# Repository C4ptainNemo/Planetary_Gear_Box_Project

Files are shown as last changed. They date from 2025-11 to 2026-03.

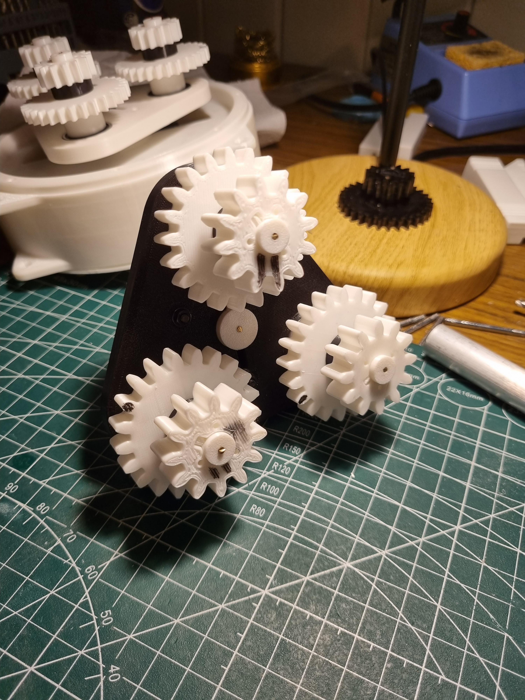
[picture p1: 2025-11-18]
PICTURES_&_DIAGRAMS/20250924_110358.jpg

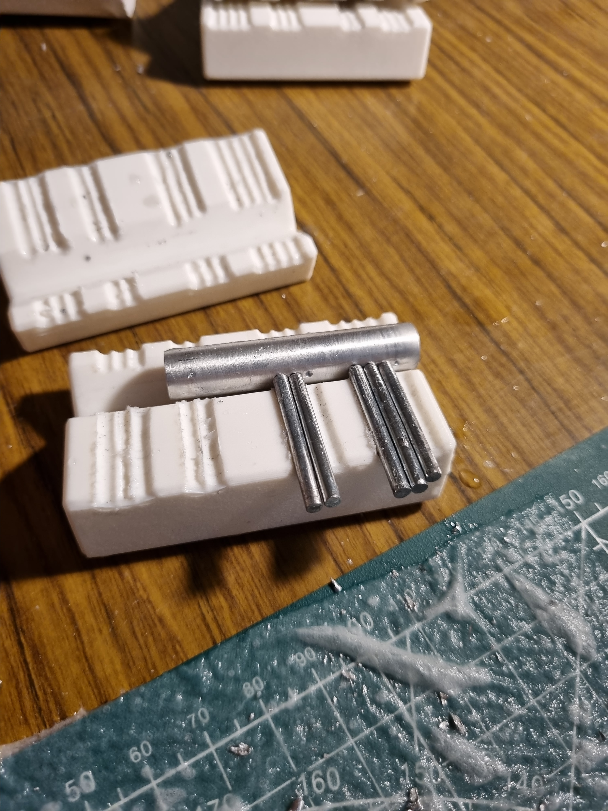
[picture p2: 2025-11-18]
PICTURES_&_DIAGRAMS/20250923_115708.jpg

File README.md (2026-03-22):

# Planetary Gear Box Project
gearbox
A Two Stage Compound Planetary Gearbox designed and built for a university design project. All content contained here was done by myself unless otherwise stated.  

The project required a gearbox that would output 20 Nm of torque and have a 65x speed reduction. This was a group project done with three others, however I did all of the CAD except for some of the technical drawings (though I have included here my own versions).

I wrote a MATLAB script to help find a solution that optimised the design to have the minimum sized gearbox. The limiting factor in the size was the minimum advised gear module (1.5) using laminated lasercut acrylic to form the gears. I will note that the code isn't very good and required some adjustment of the solution that the main script output, but it gave a decent solution that was mostly the smallest it could possibly be. The search isn't very exhaustive either, and the checks for the validity of a solution are not very compregensive nor easy to update.

My individual design is similar to the final group version that was built, with the second stage of the individual design being the same as both stages on the group design. Referencing the appendix in the individual report shows the calculations used for the individual and group gearbox.

The process of designing and building the gearbox involved:  
  1. Calculations to solve for the sun gear module of a stage (which dictated the other gear modules), given various parameters such as output torque, input speed, teeth count of all gears, factor of safety, etc.  
  2. Writing the MATLAB scripts to find a solution that minimised the size of the gearbox.  
  3. 3D printing all the parts of the gearbox, including shafts and gears to validate assembly and function, and to inform any changes that were needed.  
  4. Manufacturing the non-3D printed parts and 1-for-1 swapping them for their 3D printed counterparts.

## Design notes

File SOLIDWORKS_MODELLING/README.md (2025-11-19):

# SolidWorks Model
This is the SolidWorks directory for the gearbox assembly, subassembly and parts.  
You should just be able to download the whole directory and the relative filepaths should work fine.

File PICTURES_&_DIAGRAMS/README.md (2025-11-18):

# Pictures and Diagrams
The pictures are of the fully 3D printed prototype, as I neglected to take any of the completed gearbox (this was a lesson learned).  
The videos are of the completed gearbox with aluminium shafts and acrylic gears.

Diagrams.pptx was used to create various diagrams for the group report.
I built a basic model of the gearbox in Fusion360 (I'm more familar, and it is easier to build a simple assembly), and exported the drawings to crop and paste into Powerpoint. 
The SFD, BMD and TD plots were made with MATLAB since I'm more familiar with creating complicated plots using it.

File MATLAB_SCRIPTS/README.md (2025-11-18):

# MATLAB SCRIPTS
**1. gear_calculations.m** - The main script that takes input parameters and outputs an optimal solution.  
**2. calculate_gears.m** - Function script that does all the calculations.  
**3. individual_calculation.m** - Script that allows for inputting any number of gear teeth. This was to allow modifying a solution given by the main script.  
**4. Shaft_Force_Diagram_Plots.m** - Script for generating shaft shear force, bending moment and torque diagrams.  
**5. 251004-Planet_Gear_Table.pdf** - Gear table, showing the details about each stage.

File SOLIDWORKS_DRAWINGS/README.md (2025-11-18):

# SOLIDWORKS DRAWINGS
These are the technical drawings from SolidWorks for the gearbox. I did all of the modelling, and some of the drawings that were submitted in the report (I included my own versions here for the sake of completion).

The drawings were broken down into letter coded sections. This made it easier to delegate subassembelies and combine the individual drawings into one for the group report.

* **[A: Top Level Assembly](Top_Level_Assembly_Drawings.pdf)**
* **[B: Front Housing](Housing_Front_Assembly.pdf)**
* **[C: Middle Housing & Housing Alignment Rod](Housing_Centre_Assembly.pdf)**
* **[D: Rear Housing](Housing_Back_Assembly.pdf)**
* **[E: Stage 1 Carrier](Carrier_Stage_1.pdf)**
* **[F: Stage 2 Carrier](Carrier_Stage_2.pdf)**
* **[G: Stand](Stand_Assembly.pdf)**
* **[H: Other Parts, used in assembly](Other%20Parts.pdf)**

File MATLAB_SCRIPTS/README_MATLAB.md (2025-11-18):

1. gear_calculations - The main script that takes input parameters and outputs an optimal solution.
2. calculate_gears - Function script that does all the calculations.
3. individual_calculation - Script that allows for inputting any number of gear teeth. This was to allow modifying a solution given by the main script.
4. 251004-Planet_Gear_Table - Gear table, showing the details about each stage.

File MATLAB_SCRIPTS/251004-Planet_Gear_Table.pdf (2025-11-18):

Overall Details
Gear_ratio_total | Eff._total
________________ | __________
65.143 | 0.47292

Stage 1
Gear | | Teeth | Module_mm | Diameter_mm | Face_Width_mm | Lewis_Form_Factor | Stress_MPa | Factor_Safety | Tan._Force_N | Rad._Force_N | Torque_Nm | RPM | Power_W | V_rel_m_s
____________ | _____ | _________ | ___________ | _____________ | _________________ | __________ | _____________ | ____________ | ____________ | _________ | _______ | _______ | _________
{'Sun' | } | 15 | 1.6722 | 25.083 | 6 | 0.289 | 5.9505 | 10.083 | 17.254 | 6.2801 | 0.6492 | 1500 | 101.98 | 1.97
{'Planet 1'} | 30 | 1.6722 | 50.167 | 6 | 0.358 | 3.2661 | 18.37 | 11.732 | 4.27 | 0.29427 | -503.91 | 15.528 | 1.3236
{'Ring' | } | 57 | 1.75 | 99.75 | 6 | 0.4174 | 3.7268 | 16.1 | 16.333 | 5.9449 | 2.4439 | 0 | 0 | 0
{'Planet 2'} | 14 | 1.75 | 24.5 | 6 | 0.276 | 8.2892 | 7.2383 | 24.022 | 8.7434 | 0.29427 | -503.91 | 15.528 | 0.64642
{'Carrier' } | NaN | NaN | 75.25 | NaN | NaN | NaN | NaN | 35.754 | NaN | 4.0357 | 164.06 | 69.336 | 0.64642
Gear_Ratio | Planet_Diamater_mm | Overall_Diameter_mm | Eff._Mesh | Eff._Ack | Num_Planets | Safety_Factor | S_y_MPa | Pressure_Angle_deg
__________ | __________________ | ___________________ | _________ | ________ | ___________ | _____________ | _______ | __________________
9.1429 | 125.42 | 125.42 | 0.75 | 0.67993 | 3 | 3 | 60 | 20

Stage 2
Gear | | Teeth | Module_mm | Diameter_mm | Face_Width_mm | Lewis_Form_Factor | Stress_MPa | Factor_Safety | Tan._Force_N | Rad._Force_N | Torque_Nm | RPM | Power_W | V_rel_m_s
____________ | _____ | _________ | ___________ | _____________ | _________________ | __________ | _____________ | ____________ | ____________ | _________ | _______ | _______ | _________
{'Sun' | } | 12 | 2.2727 | 27.273 | 9 | 0.245 | 19.686 | 3.0479 | 98.651 | 35.906 | 4.0357 | 164.06 | 69.336 | 0.23428
{'Planet 1'} | 21 | 2.2727 | 47.727 | 9 | 0.325 | 10.322 | 5.813 | 68.616 | 24.974 | 1.6374 | -57.566 | 9.8709 | 0.14386
{'Ring' | } | 42 | 2.5 | 105 | 9 | 0.393 | 8.5865 | 6.9877 | 75.926 | 27.635 | 11.958 | 0 | 0 | 0
{'Planet 2'} | 12 | 2.5 | 30 | 9 | 0.245 | 19.803 | 3.0299 | 109.16 | 39.732 | 1.6374 | -57.566 | 9.8709 | 0.090424
{'Carrier' } | NaN | NaN | 75 | NaN | NaN | NaN | NaN | 177.78 | NaN | 20 | 23.026 | 48.226 | 0.090424
Gear_Ratio | Planet_Diamater_mm | Overall_Diameter_mm | Eff._Mesh | Eff._Ack | Num_Planets | Safety_Factor | S_y_MPa | Pressure_Angle_deg
__________ | __________________ | ___________________ | _________ | ________ | ___________ | _____________ | _______ | __________________
7.125 | 122.73 | 122.73 | 0.75 | 0.69554 | 3 | 3 | 60 | 20

>>

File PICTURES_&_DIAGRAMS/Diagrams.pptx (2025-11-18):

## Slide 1

y

x

F_(R,s)

F_(t,s)

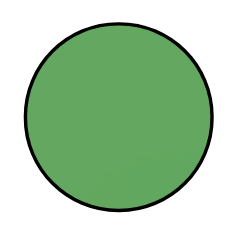
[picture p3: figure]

ω_s , T_s

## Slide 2

y

x

F_(t,c)

F_(t,c)

ω_s , T_s

r_c

F_(t,c)

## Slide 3

y

x

F_(R,p_2)

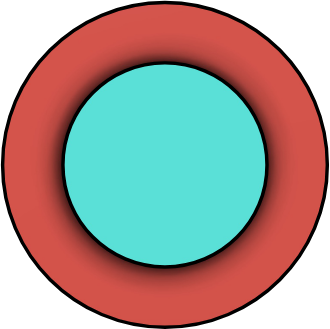
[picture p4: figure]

F_(t,p_2)

F_(t,c)

F_(t,p_1)

ω_s

ω_p

F_(R,p_1)

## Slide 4

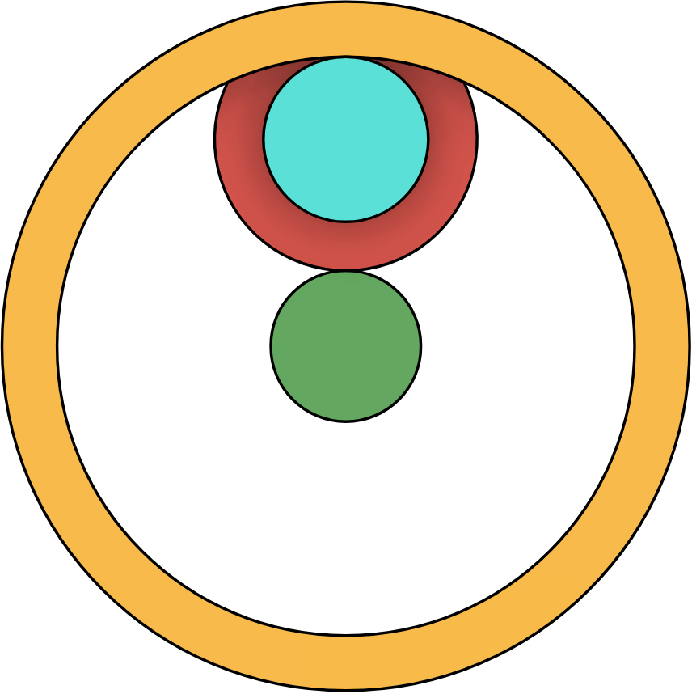
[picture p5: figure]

r_(p_2)

r_(p_1)

r_r

r_s

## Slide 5

F_(R,p_2)

F_(t,p_2)

y

x

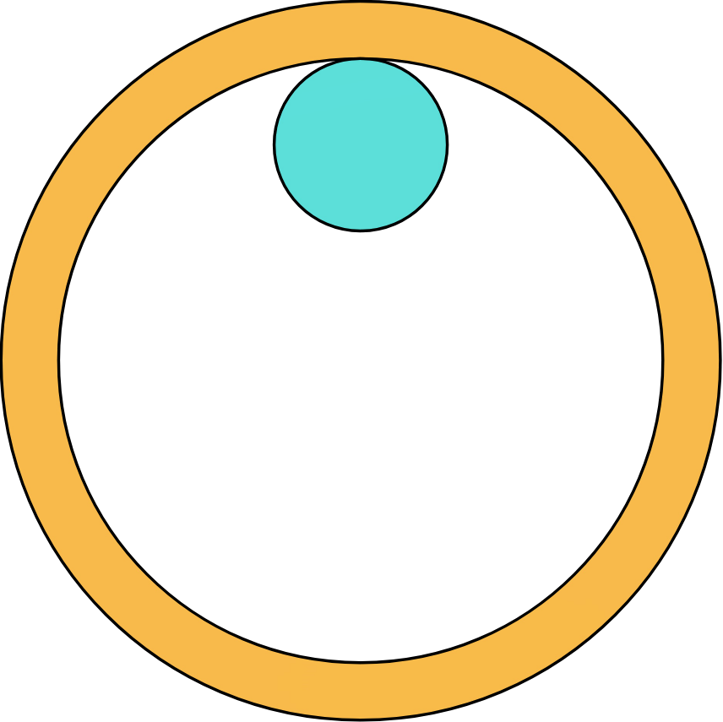
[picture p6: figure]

F_(t,r)

F_(R,r)

ω_p

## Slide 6

y

x

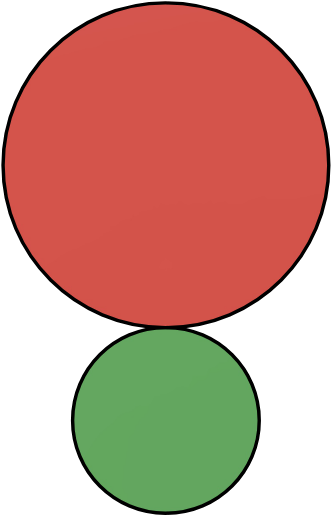
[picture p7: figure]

v_c

ω_c

v_p^(′)

ω_s

ω_p

v_s

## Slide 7

y

x

v_p^(′)

ω_c

v_c

ω_p

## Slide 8

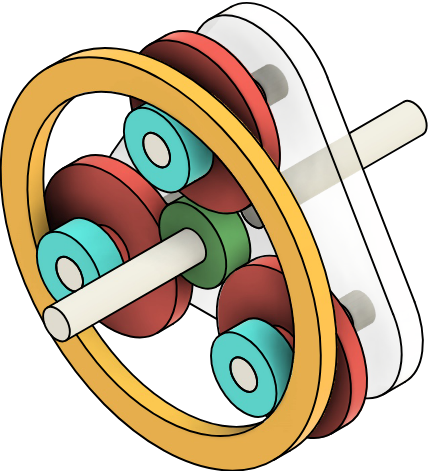
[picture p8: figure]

y

x

z

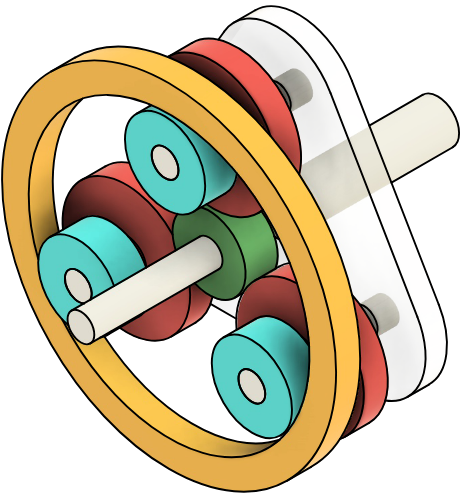
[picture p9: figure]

y

x

z

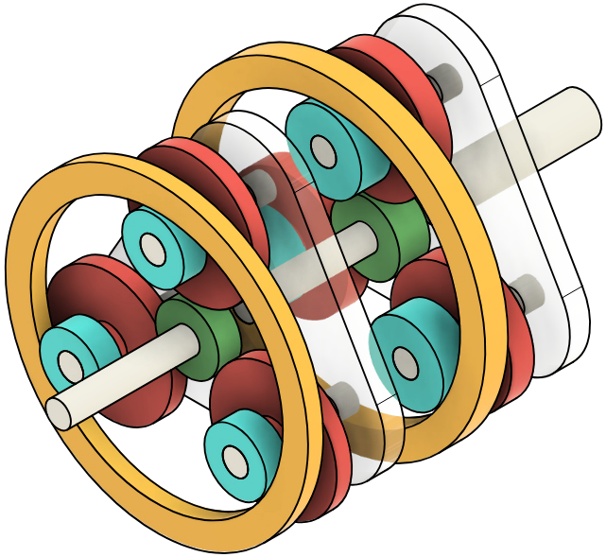
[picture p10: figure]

y

x

z

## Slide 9

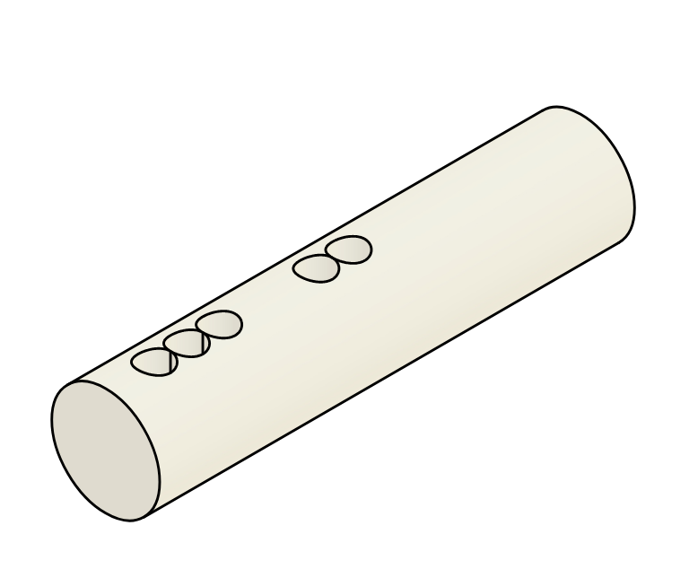
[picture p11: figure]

y

x

z

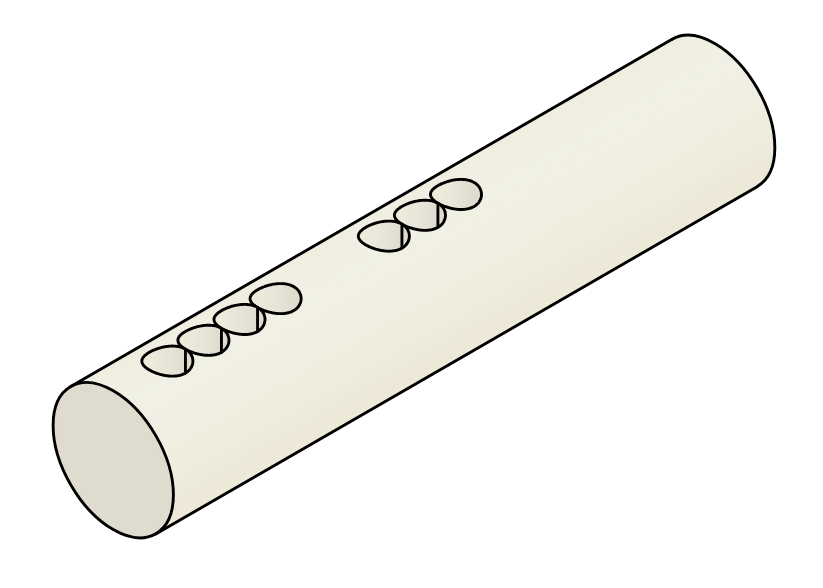
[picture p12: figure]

y

x

z

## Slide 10

y

y

z

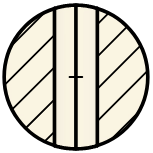
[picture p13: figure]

z

y

z

x

z

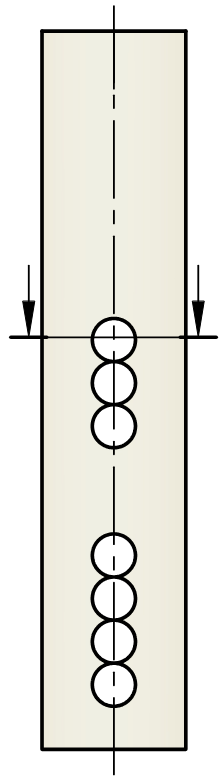
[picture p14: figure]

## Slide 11

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
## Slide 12

y

x

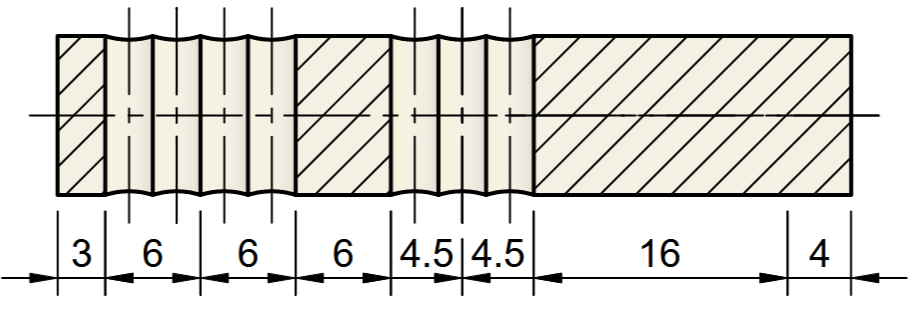
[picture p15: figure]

y

x

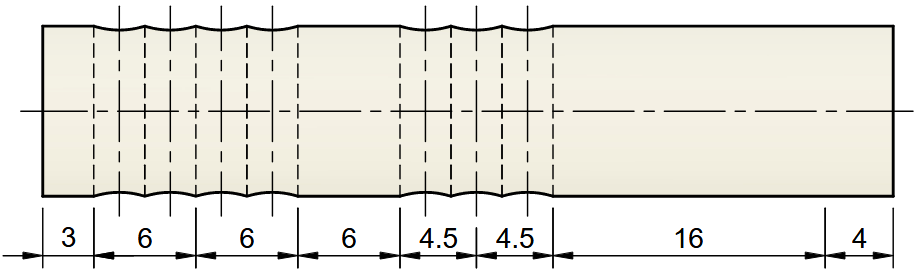
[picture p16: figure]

x

z

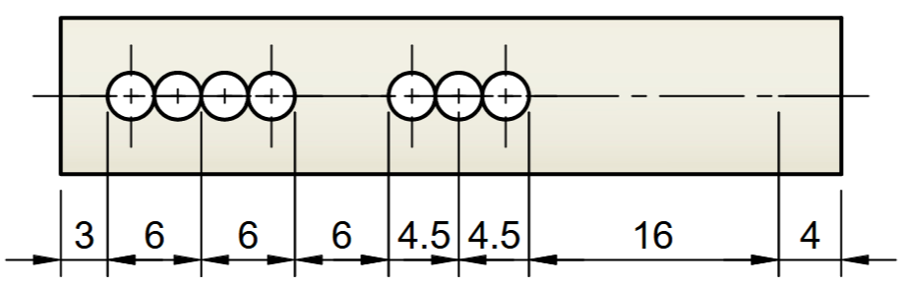
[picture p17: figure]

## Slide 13

y

x

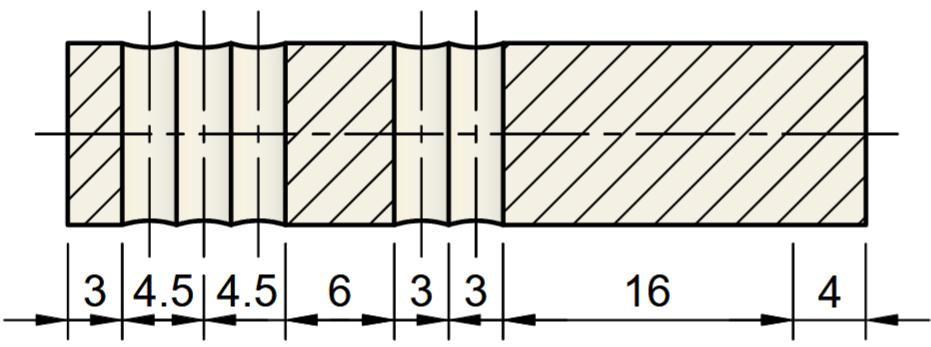
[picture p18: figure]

y

x

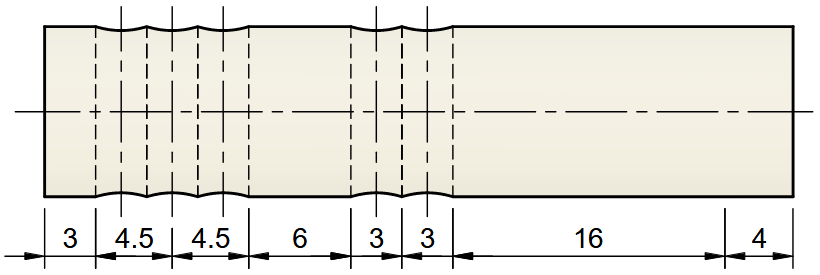
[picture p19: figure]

x

z

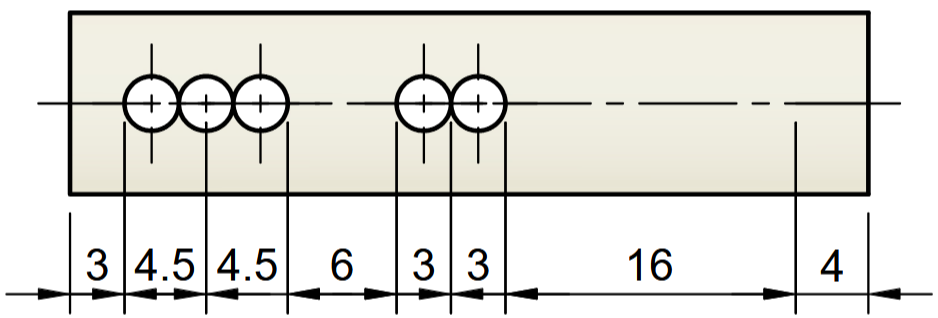
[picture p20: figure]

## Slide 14

y

x

y

x

y

x

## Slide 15

y

x

F_(R,p_2)

F_(R,p_1)

R_y

M_(D,z)

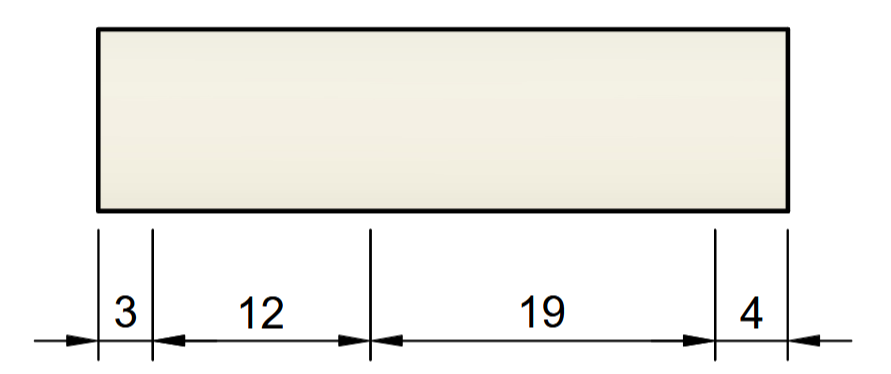
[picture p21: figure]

A

B

C

D

R_x

T_(p_2)

T_(p_1)

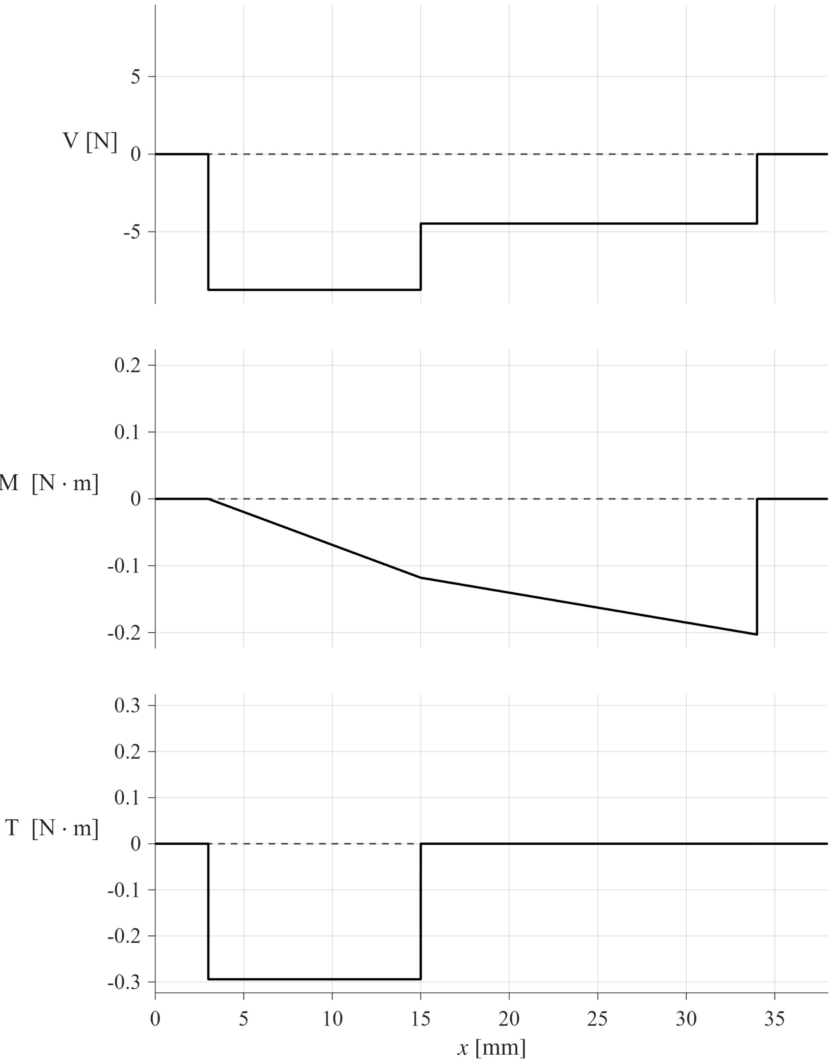
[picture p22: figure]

7.5

13.5

19

4

x

z

F_(t,p_2)

F_(t,p_1)

R_z

M_(D,y)

R_x

A

B

C

D

T_(p_2)

T_(p_1)

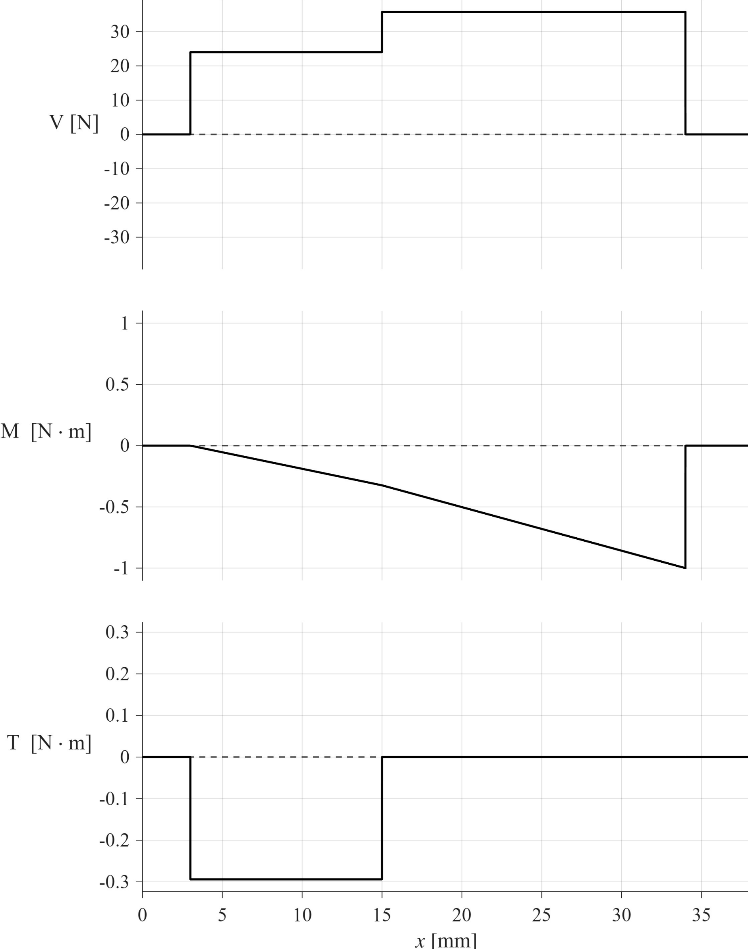
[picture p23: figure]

7.5

13.5

19

4

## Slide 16

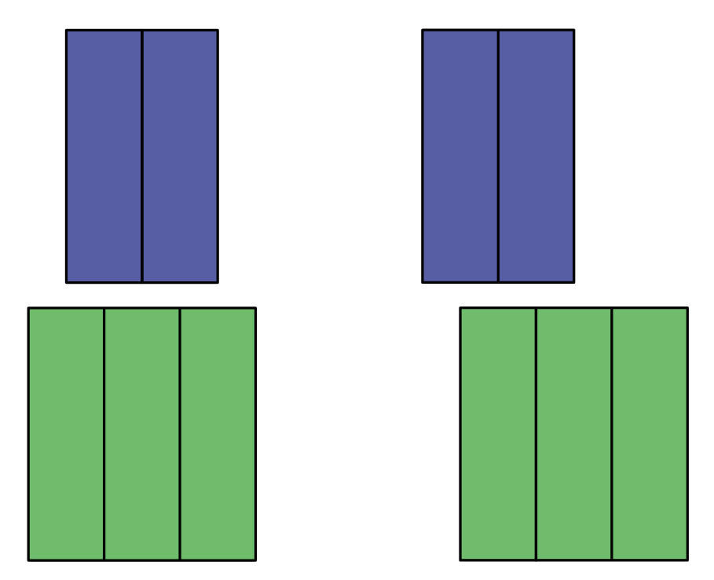
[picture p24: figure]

Aligned

Misaligned

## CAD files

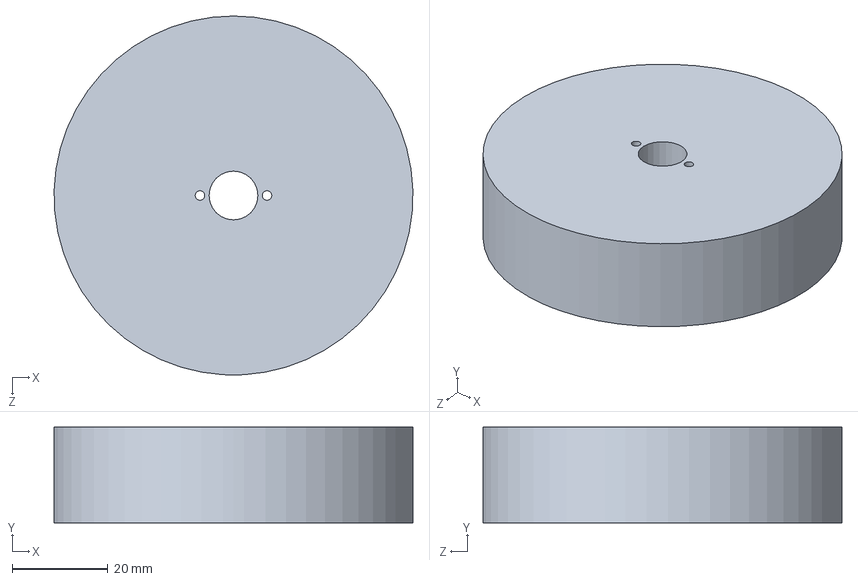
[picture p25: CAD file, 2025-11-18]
SOLIDWORKS_MODELLING/Assembly Parts/Gear Assembly Stand.SLDPRT
75.0 x 20.0 x 75.0 mm

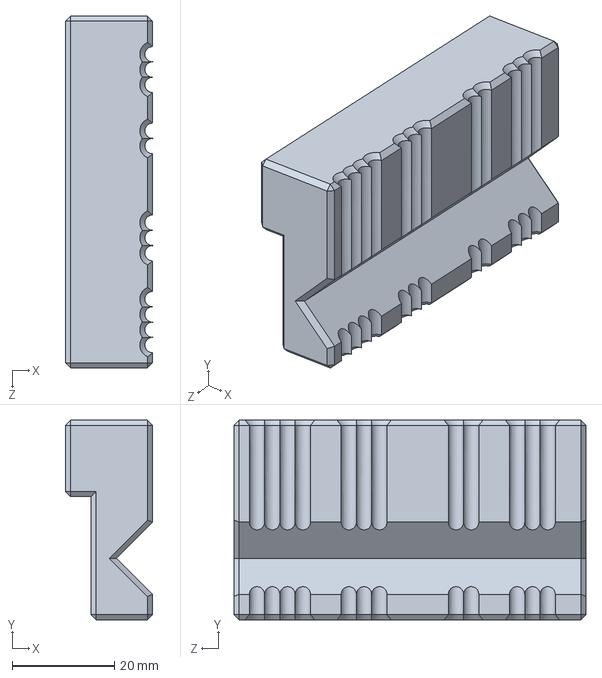
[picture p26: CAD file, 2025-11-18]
SOLIDWORKS_MODELLING/Assembly Parts/Drill Hole Guide.SLDPRT
17.1 x 39.1 x 69.0 mm

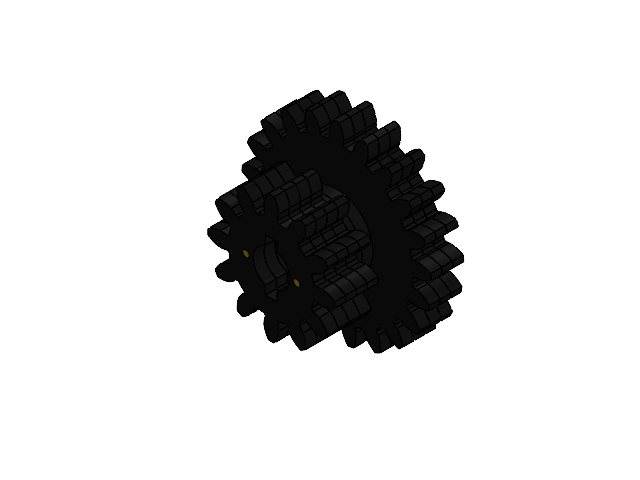
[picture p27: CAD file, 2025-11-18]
SOLIDWORKS_MODELLING/Assemblies/Gears/Planet_Gear_Stage_2.SLDASM
External_Spur_Gear x 7
Spacer x 2
Alignment_Pin x 2

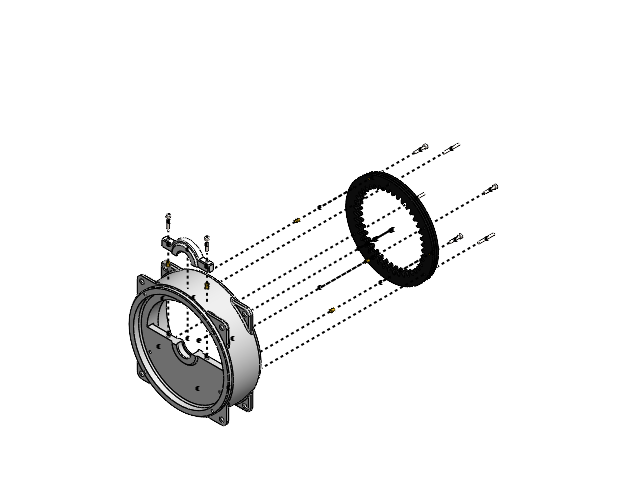
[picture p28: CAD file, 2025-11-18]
SOLIDWORKS_MODELLING/Assemblies/Housing_Centre_Assembly.SLDASM
Housing_Centre
Housing_Bearing_Cover
Threaded_Heat_Insert_M3x5.7x4.6 x 5
Internal_Spur_Gear_Stage_2 x 3
Alignment_Pin x 3
socket head cap screw_iso x 5
Ring_Gear_Alignment_Pin x 3

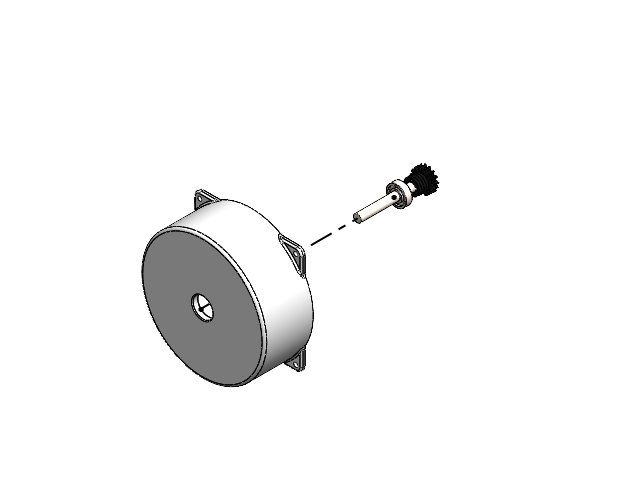
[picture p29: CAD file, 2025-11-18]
SOLIDWORKS_MODELLING/Gearbox-2_Stage-Planetary_Compound-65_Reduction.SLDASM
Housing_Front
Threaded_Heat_Insert_M3x5.7x4.6 x 3
Internal_Spur_Gear_Stage_1 x 2
Alignment_Pin x 5
socket head cap screw_iso x 3
Ring_Gear_Alignment_Pin x 3
Shaft_KeyPins_SingleEnded
Key_Pin_3mm x 3
External_Spur_Gear x 3
Spacer x 4
radial ball bearing_68_skf

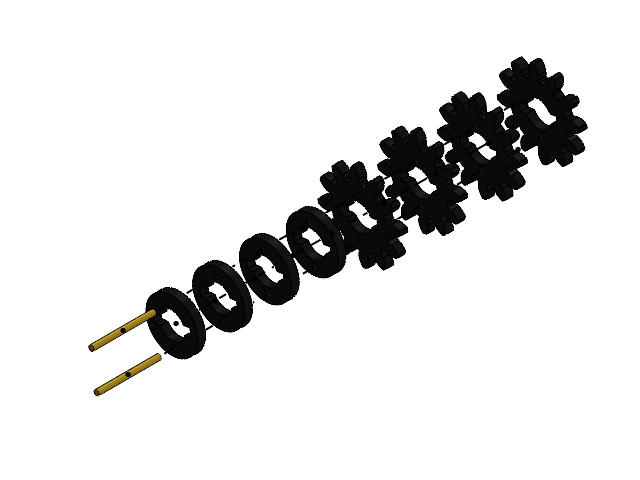
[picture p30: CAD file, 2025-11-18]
SOLIDWORKS_MODELLING/Assemblies/Gears/Sun_Gear_2.SLDASM
External_Spur_Gear x 4
Alignment_Pin x 2
Spacer x 4

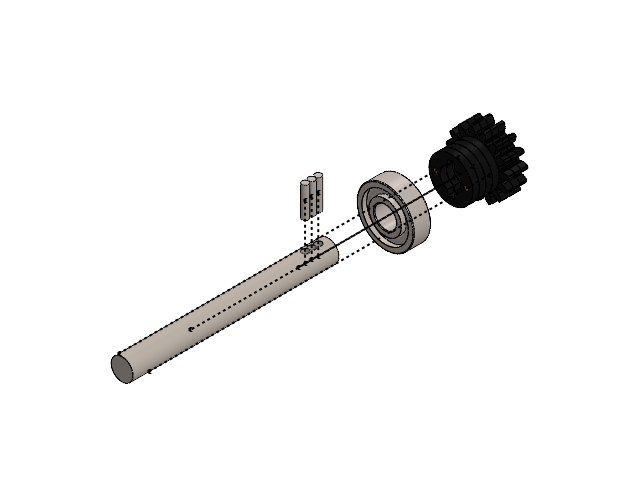
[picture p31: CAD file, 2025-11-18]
SOLIDWORKS_MODELLING/Assemblies/Sun_Gear_Stage_1_Subassembly.SLDASM
Shaft_KeyPins_SingleEnded
Key_Pin_3mm x 3
External_Spur_Gear x 3
Alignment_Pin x 2
Spacer x 4
radial ball bearing_68_skf

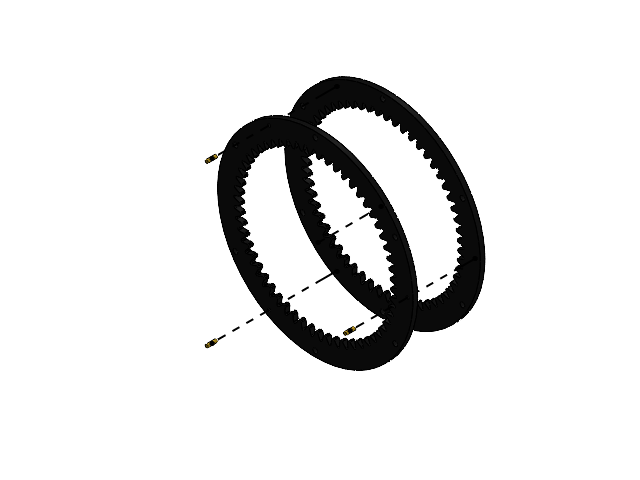
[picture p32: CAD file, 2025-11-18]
SOLIDWORKS_MODELLING/Assemblies/Gears/Ring_Gear_Stage_1.SLDASM
Internal_Spur_Gear_Stage_1 x 2
Alignment_Pin x 3

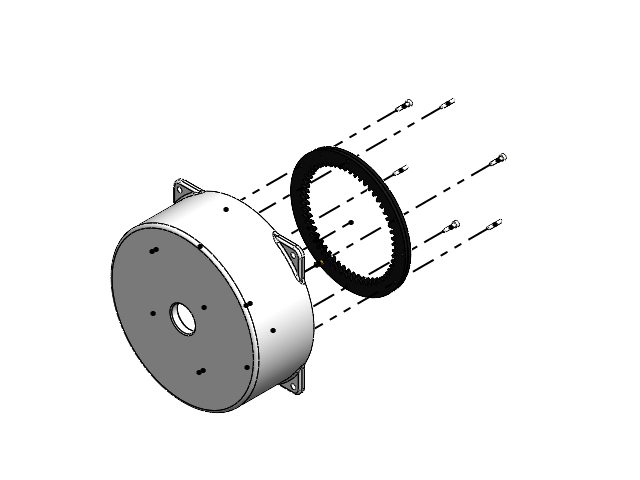
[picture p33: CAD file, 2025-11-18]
SOLIDWORKS_MODELLING/Assemblies/Housing_Front_Assembly.SLDASM
Housing_Front
Threaded_Heat_Insert_M3x5.7x4.6 x 3
Internal_Spur_Gear_Stage_1 x 2
Alignment_Pin x 3
socket head cap screw_iso x 3
Ring_Gear_Alignment_Pin x 3

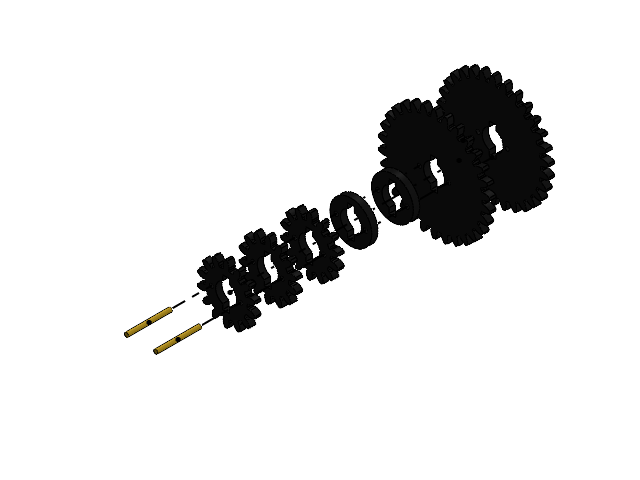
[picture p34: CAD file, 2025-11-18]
SOLIDWORKS_MODELLING/Assemblies/Gears/Planet_Gear_Stage_1.SLDASM
External_Spur_Gear x 5
Spacer x 2
Alignment_Pin x 2

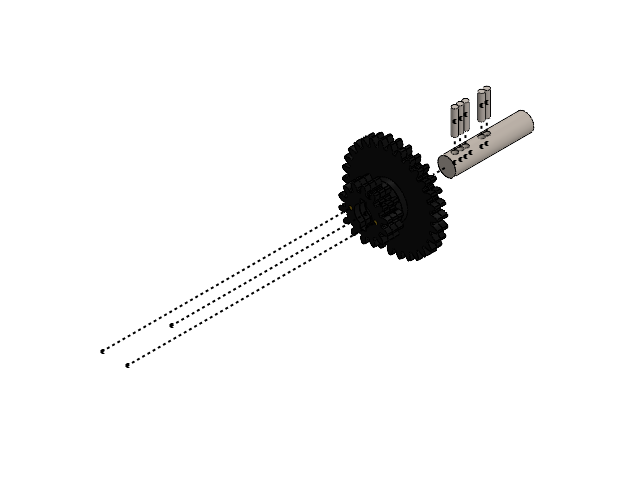
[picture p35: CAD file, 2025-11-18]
SOLIDWORKS_MODELLING/Assemblies/Planet_Gear_Stage_1_Subassembly.SLDASM
Shaft_KeyPins_SingleEnded
Key_Pin_3mm x 5
External_Spur_Gear x 5
Spacer x 2
Alignment_Pin x 2

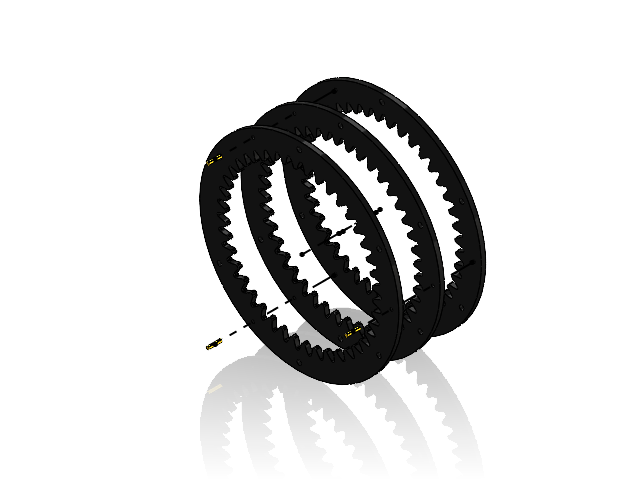
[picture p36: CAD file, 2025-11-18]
SOLIDWORKS_MODELLING/Assemblies/Gears/Ring_Gear_Stage_2.SLDASM
Internal_Spur_Gear_Stage_2 x 3
Alignment_Pin x 3

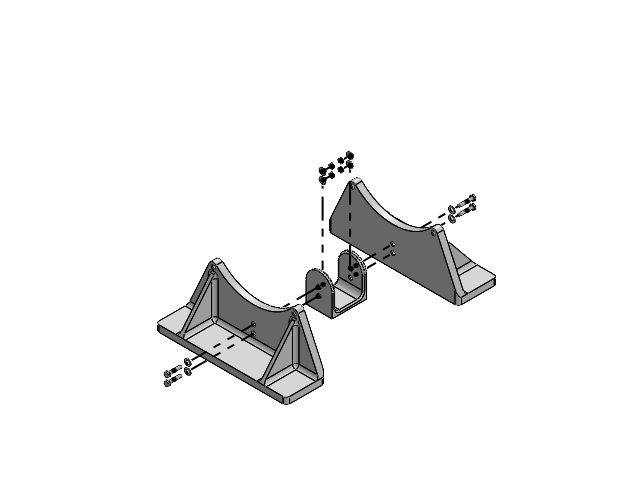
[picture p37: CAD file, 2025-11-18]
SOLIDWORKS_MODELLING/Assemblies/Stand_Assembly.SLDASM
Stand x 2
Stand_Spacer
plain washer 10669 type nl_iso x 8
hex bolt gradeb_iso x 4
hex thin nut chamfered gradeab_iso x 4

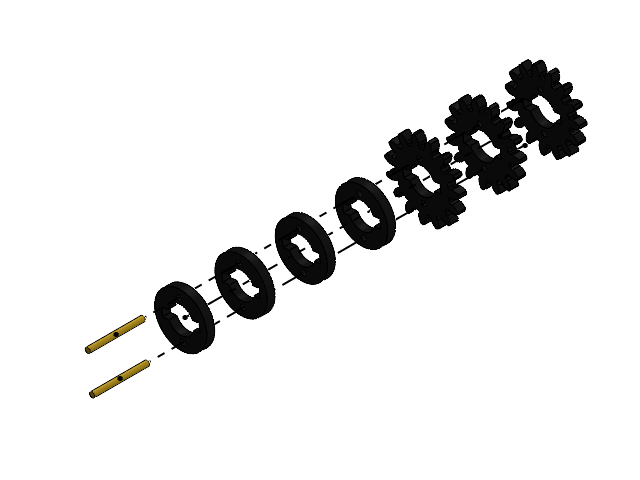
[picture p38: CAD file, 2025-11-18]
SOLIDWORKS_MODELLING/Assemblies/Gears/Sun_Gear_1.SLDASM
External_Spur_Gear x 3
Alignment_Pin x 2
Spacer x 4

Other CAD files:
SOLIDWORKS_MODELLING/Assemblies/Housing_Back_Assembly.SLDASM
SOLIDWORKS_MODELLING/Assemblies/Carrier_Stage_2.SLDASM
SOLIDWORKS_MODELLING/Assemblies/Planet_Gear_Stage_2_Subassembly.SLDASM
SOLIDWORKS_MODELLING/Assemblies/Carrier_Stage_1.SLDASM
SOLIDWORKS_MODELLING/Assembly Parts/12 mm Half Spacer.SLDPRT
SOLIDWORKS_MODELLING/Assembly Parts/Bearing Removal Plate.SLDPRT
SOLIDWORKS_MODELLING/Assembly Parts/Bearing Removal Stand.SLDPRT
SOLIDWORKS_MODELLING/Assembly Parts/Drill Hole Guide Double Ended.SLDPRT
SOLIDWORKS_MODELLING/Assembly Parts/Drill Hole Guide large.SLDPRT
SOLIDWORKS_MODELLING/Assembly Parts/Pulley.SLDPRT
SOLIDWORKS_MODELLING/Parts/Carrier/Carrier.SLDPRT
SOLIDWORKS_MODELLING/Parts/Carrier/Carrier_Retainer_Plate.SLDPRT
SOLIDWORKS_MODELLING/Parts/Gears/Alignment_Pin.SLDPRT
SOLIDWORKS_MODELLING/Parts/Gears/External_Spur_Gear.SLDPRT
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

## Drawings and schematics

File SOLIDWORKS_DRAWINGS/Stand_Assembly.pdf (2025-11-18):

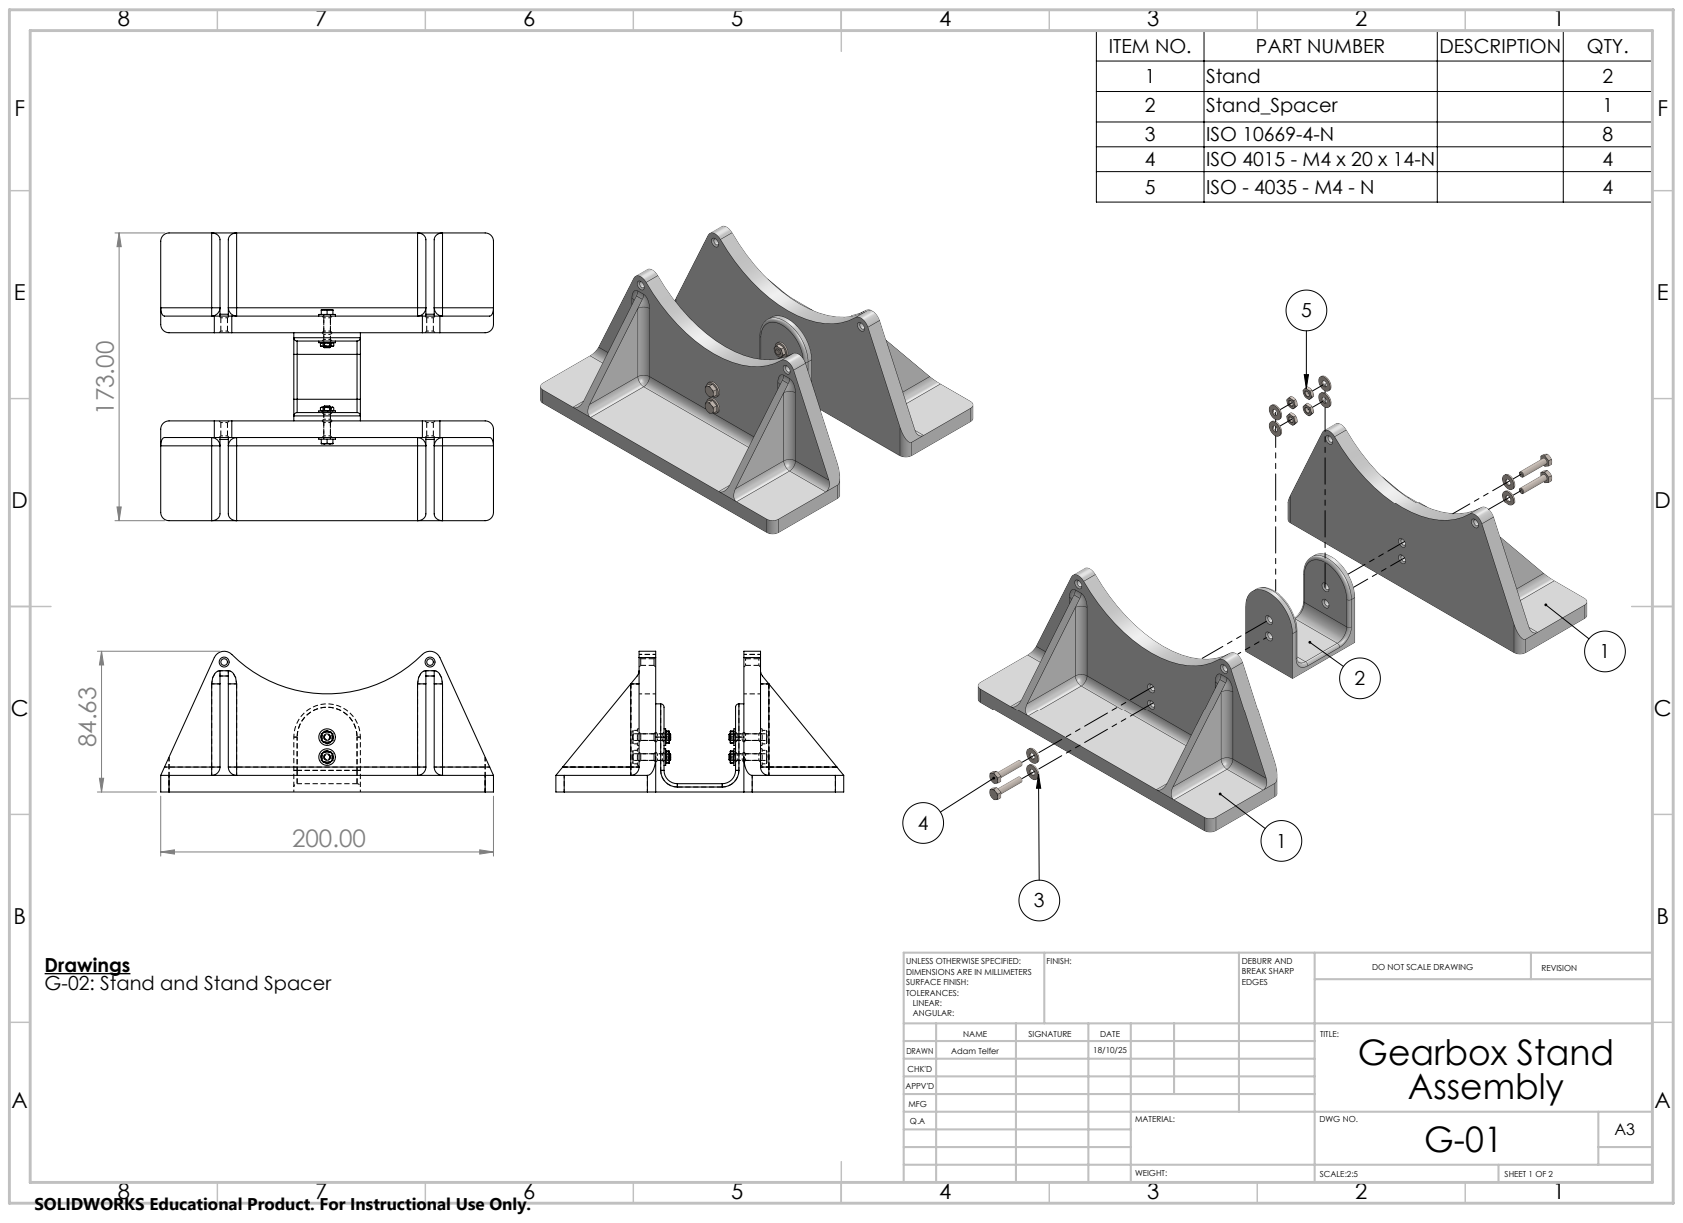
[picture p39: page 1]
FINISH:; DEBURR AND; BREAK SHARP; DO NOT SCALE DRAWING; REVISION; SCALE:2:5; SHEET 1 OF 2; Assembly A

ITEM NO. | PART NUMBER | DESCRIPTION | QTY.
1 | Stand | | 2
2 | Stand_Spacer | | 1
3 | ISO 10669-4-N | | 8
4 | ISO 4015 - M4 x 20 x 14-N | | 4
5 | ISO - 4035 - M4 - N | | 4

Drawings
G-02: Stand and Stand Spacer

UNLESS OTHERWISE SPECIFIED:
DIMENSIONS ARE IN MILLIMETERS
SURFACE FINISH:
TOLERANCES:
LINEAR:
ANGULAR:

NAME | SIGNATURE | DATE | | | | TITLE: Gearbox Stand

DRAWN | Adam Telfer | | 18/10/25
CHK'D
APPV'D
MFG
Q.A | | | | MATERIAL: | DWG NO. G-01 | A3

SOLIDWORKS Educational Product. For Instructional Use Only.

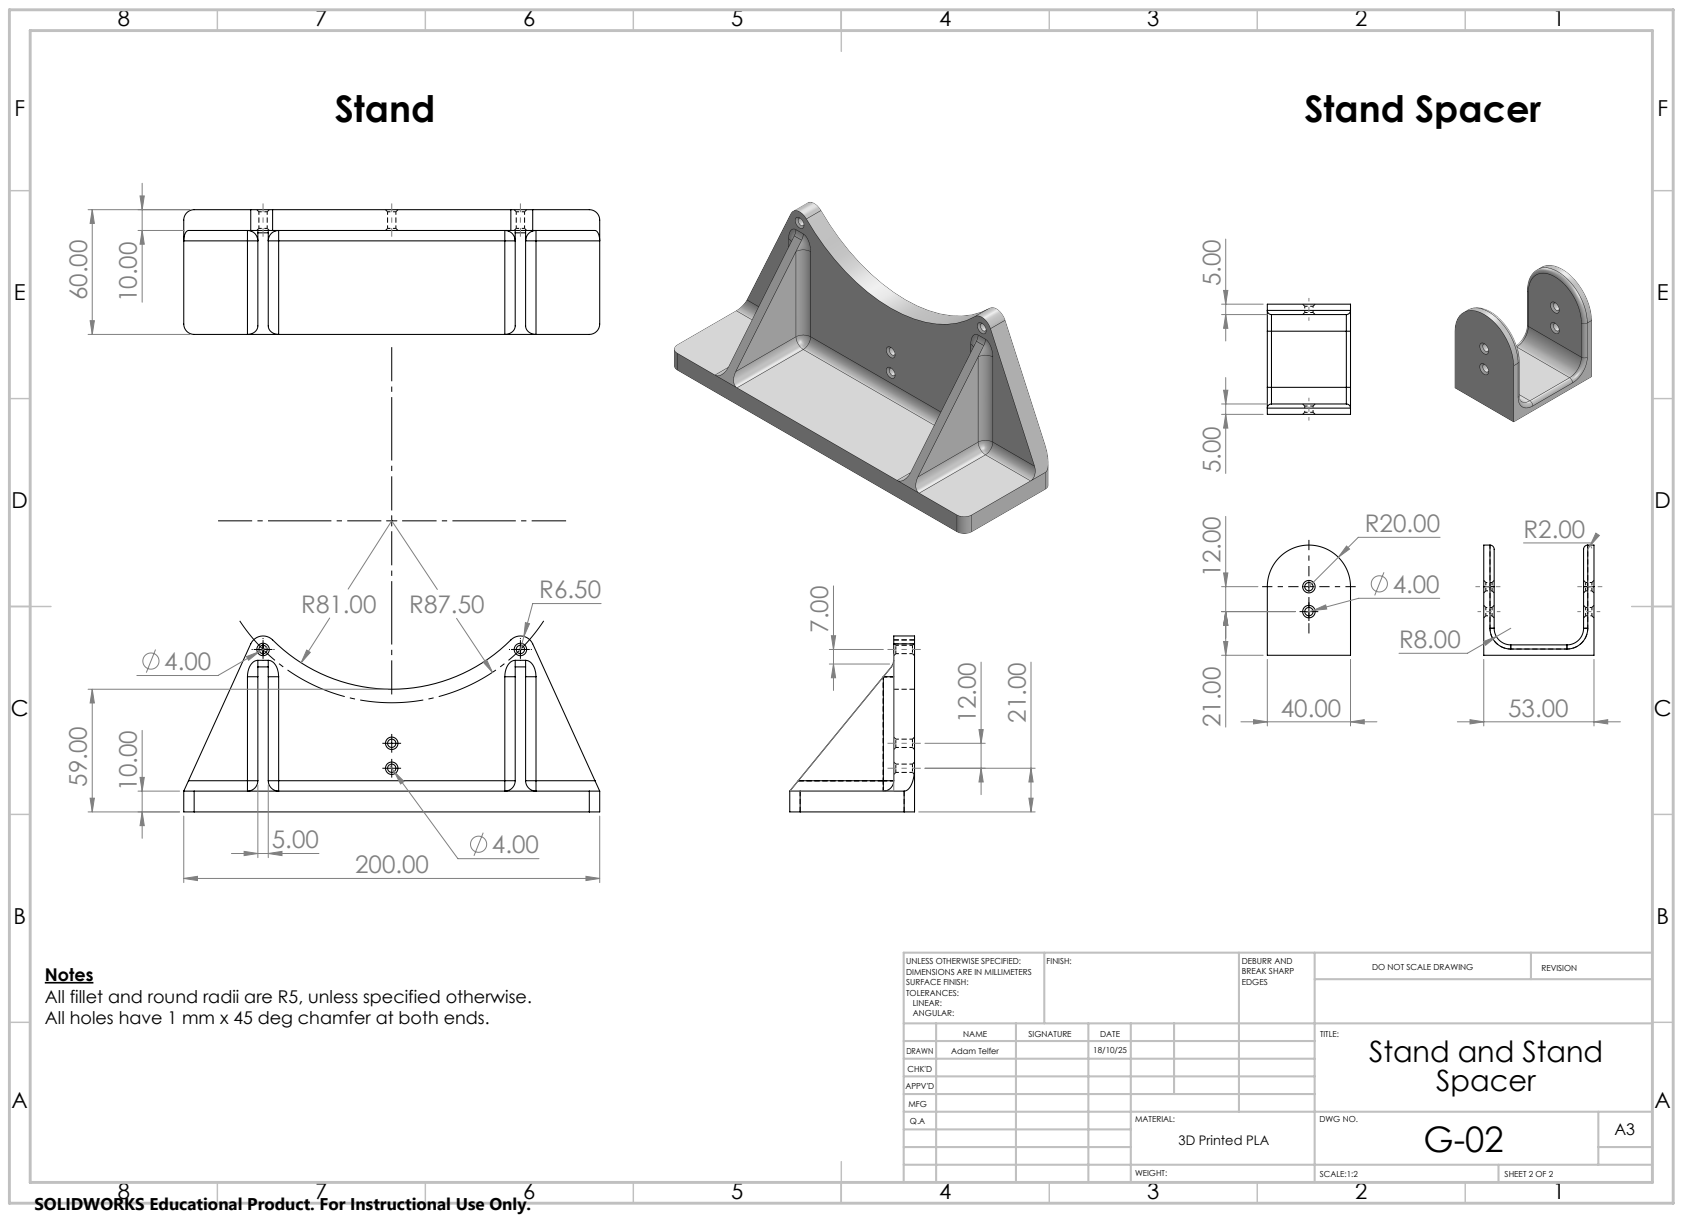
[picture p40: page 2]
Stand; Stand Spacer; FINISH:; DEBURR AND; BREAK SHARP; DO NOT SCALE DRAWING; REVISION; SCALE:1:2; SHEET 2 OF 2; Spacer A

UNLESS OTHERWISE SPECIFIED:
DIMENSIONS ARE IN MILLIMETERS
SURFACE FINISH:
TOLERANCES:
LINEAR:
ANGULAR:

Notes
All fillet and round radii are R5, unless specified otherwise.
All holes have 1 mm x 45 deg chamfer at both ends.

NAME | SIGNATURE | DATE | | | | TITLE: Stand and Stand

DRAWN | Adam Telfer | | 18/10/25
CHK'D
APPV'D
MFG
Q.A | | | | MATERIAL: | DWG NO. G-02 | A3 3D Printed PLA

SOLIDWORKS Educational Product. For Instructional Use Only.

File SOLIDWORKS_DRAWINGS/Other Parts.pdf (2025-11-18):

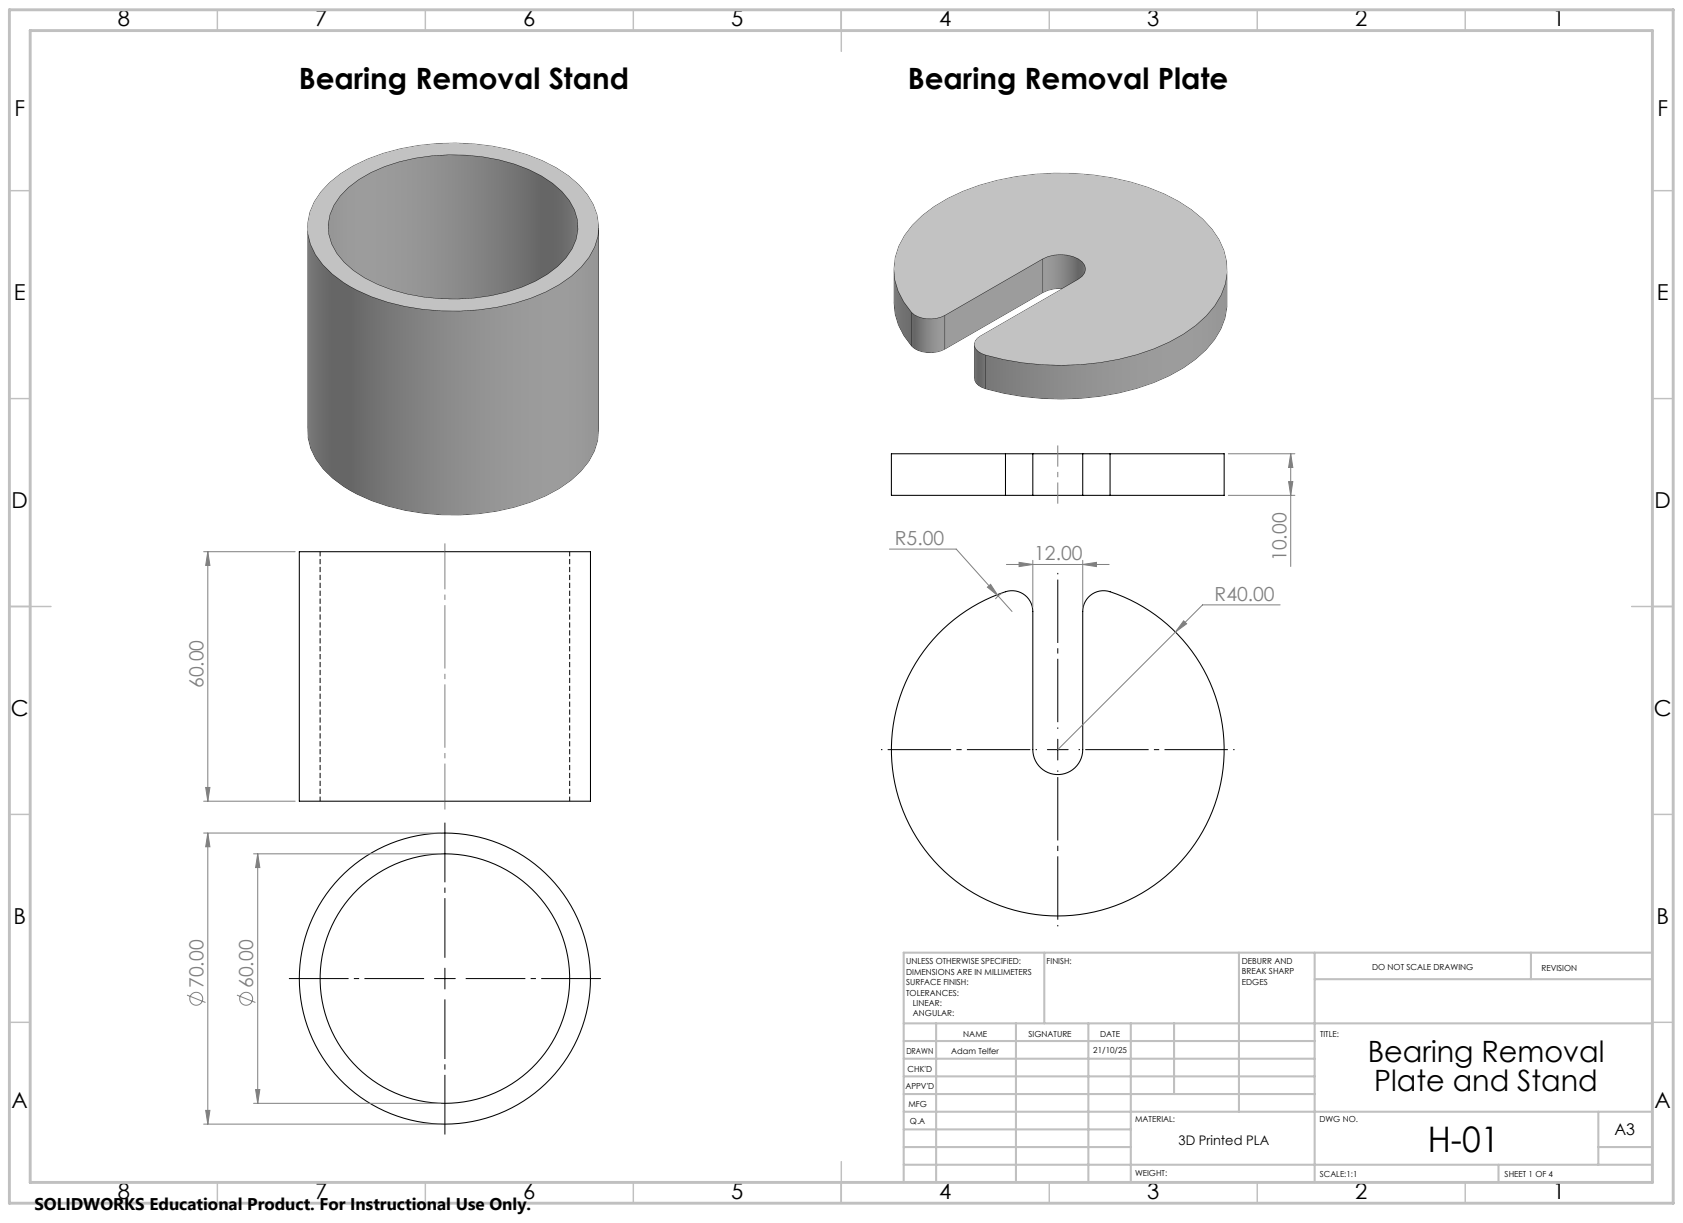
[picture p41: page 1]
Bearing Removal Stand; Bearing Removal Plate; FINISH:; DEBURR AND; BREAK SHARP; DO NOT SCALE DRAWING; REVISION; SCALE:1:1; SHEET 1 OF 4

UNLESS OTHERWISE SPECIFIED:
DIMENSIONS ARE IN MILLIMETERS
SURFACE FINISH:
TOLERANCES:
LINEAR:
ANGULAR:

NAME | SIGNATURE | DATE | | | | TITLE: Bearing Removal Plate and Stand

DRAWN | Adam Telfer | | 21/10/25
CHK'D
APPV'D
MFG
Q.A | | | | MATERIAL: | DWG NO. H-01 | A3 3D Printed PLA

SOLIDWORKS Educational Product. For Instructional Use Only.

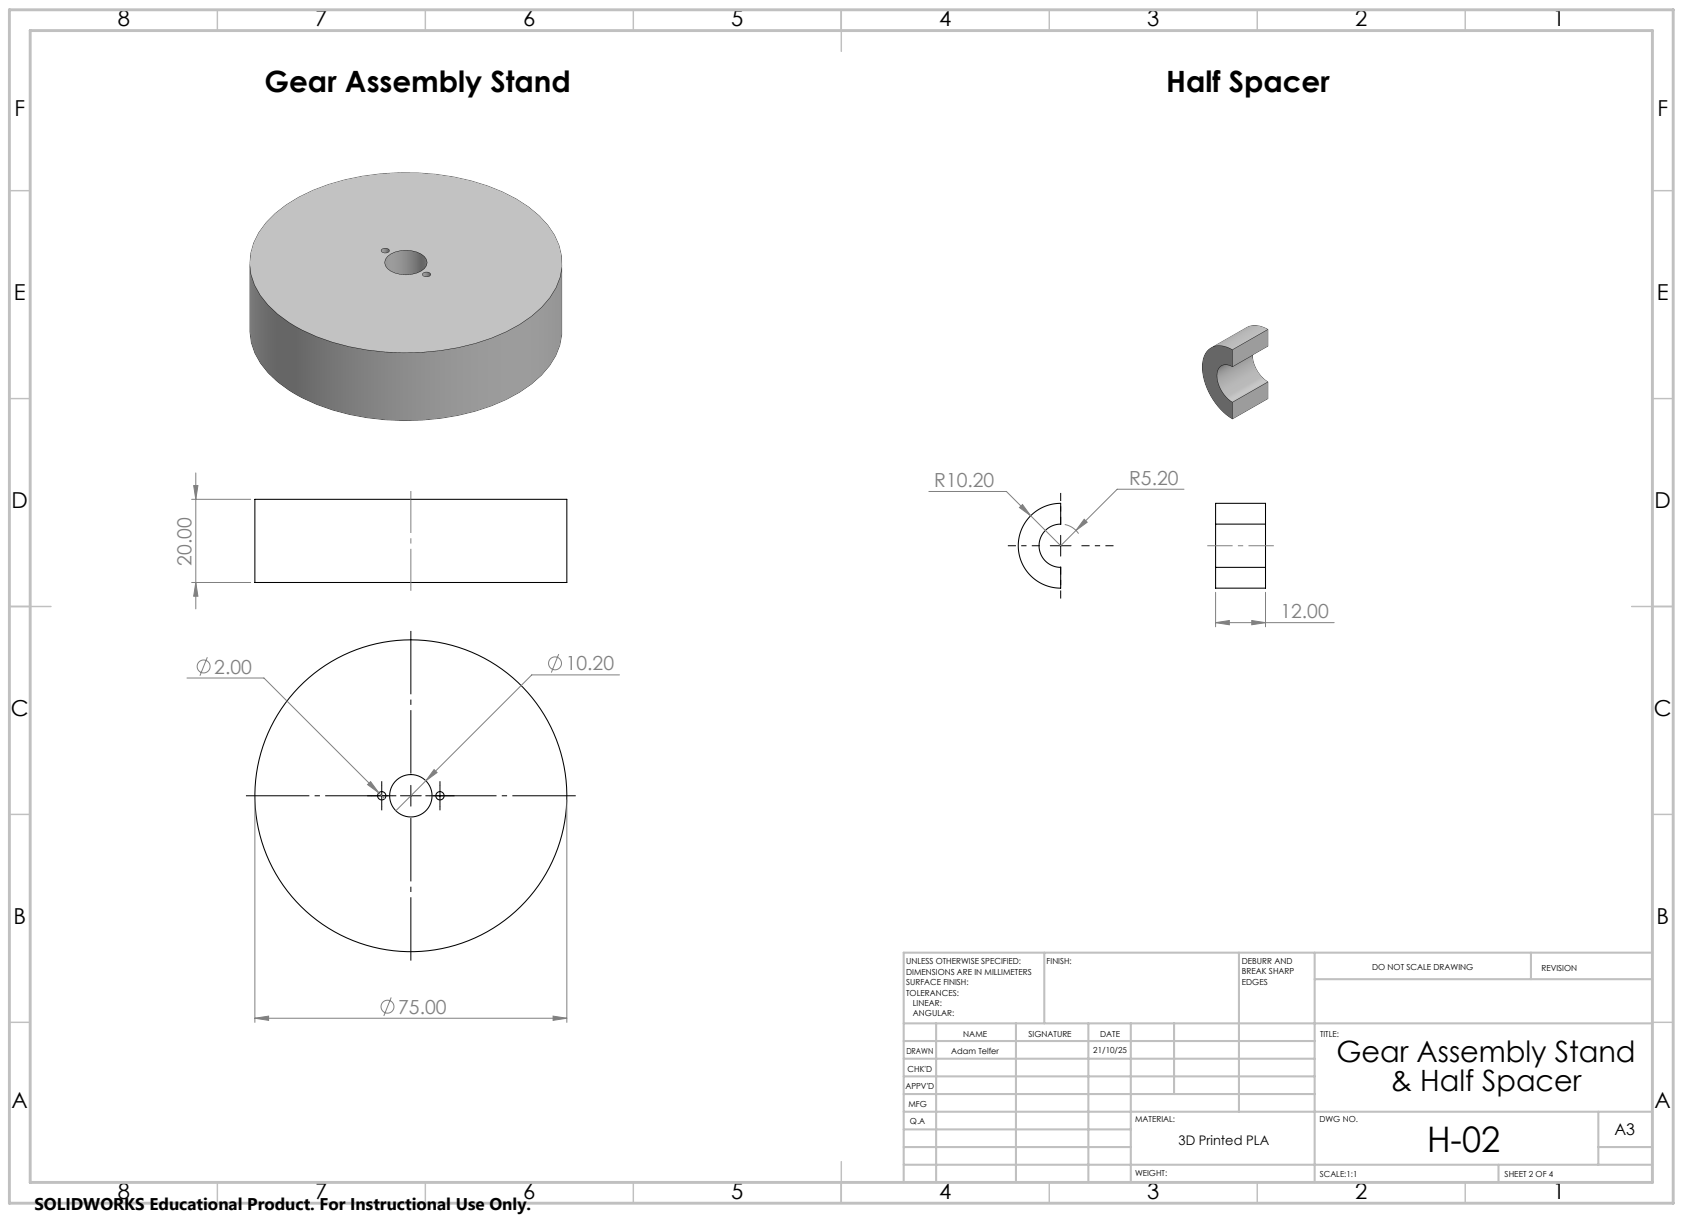
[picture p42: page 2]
Gear Assembly Stand; Half Spacer; FINISH:; DEBURR AND; BREAK SHARP; DO NOT SCALE DRAWING; REVISION; & Half Spacer A

UNLESS OTHERWISE SPECIFIED:
DIMENSIONS ARE IN MILLIMETERS
SURFACE FINISH:
TOLERANCES:
LINEAR:
ANGULAR:

NAME | SIGNATURE | DATE | TITLE: Gear Assembly Stand

DRAWN | Adam Telfer | | 21/10/25
CHK'D
APPV'D
MFG

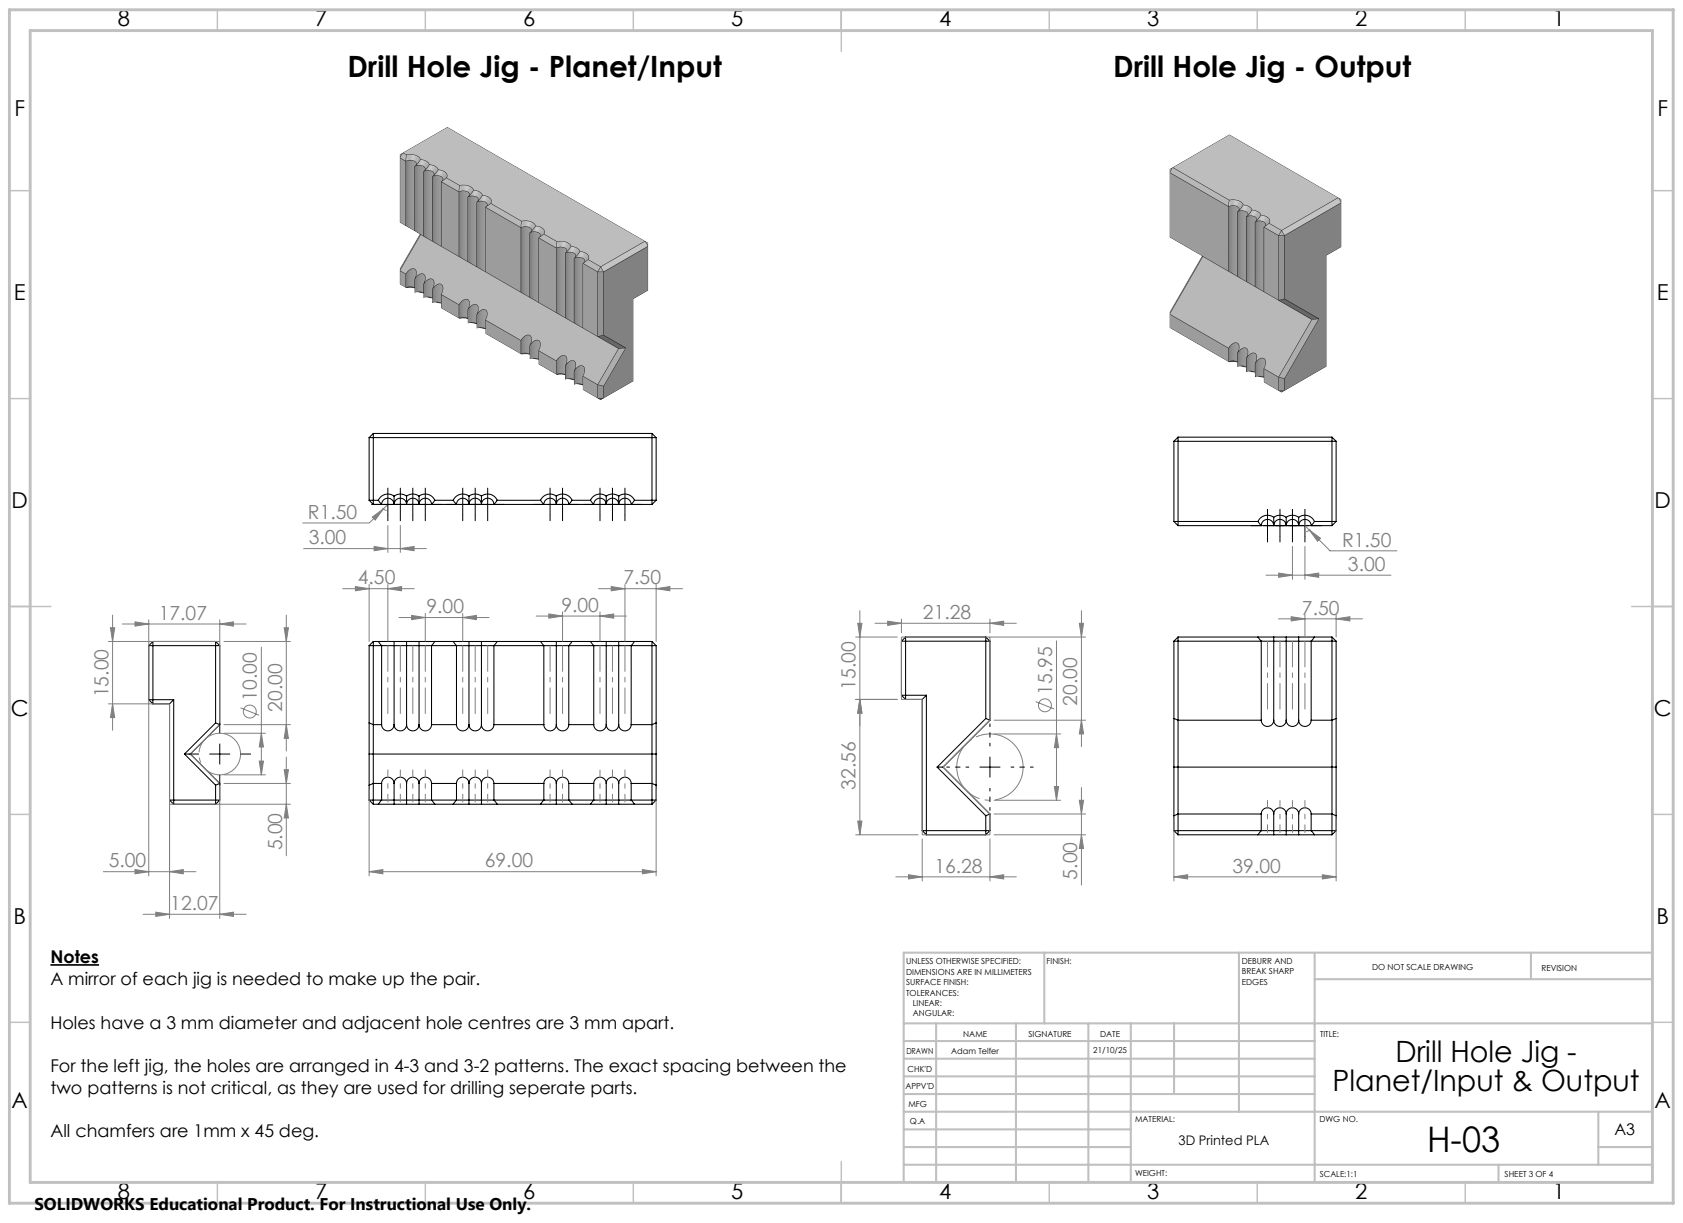
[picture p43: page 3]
Drill Hole Jig - Planet/Input; Drill Hole Jig - Output; FINISH:; DEBURR AND; BREAK SHARP; DO NOT SCALE DRAWING; REVISION; Planet/Input & Output A

Notes
A mirror of each jig is needed to make up the pair.
Holes have a 3 mm diameter and adjacent hole centres are 3 mm apart.
For the left jig, the holes are arranged in 4-3 and 3-2 patterns. The exact spacing between the
two patterns is not critical, as they are used for drilling seperate parts.
All chamfers are 1mm x 45 deg.

UNLESS OTHERWISE SPECIFIED:
DIMENSIONS ARE IN MILLIMETERS
SURFACE FINISH:
TOLERANCES:
LINEAR:
ANGULAR:

NAME | SIGNATURE | DATE | TITLE: Drill Hole Jig -

DRAWN | Adam Telfer | | 21/10/25
CHK'D
APPV'D
MFG

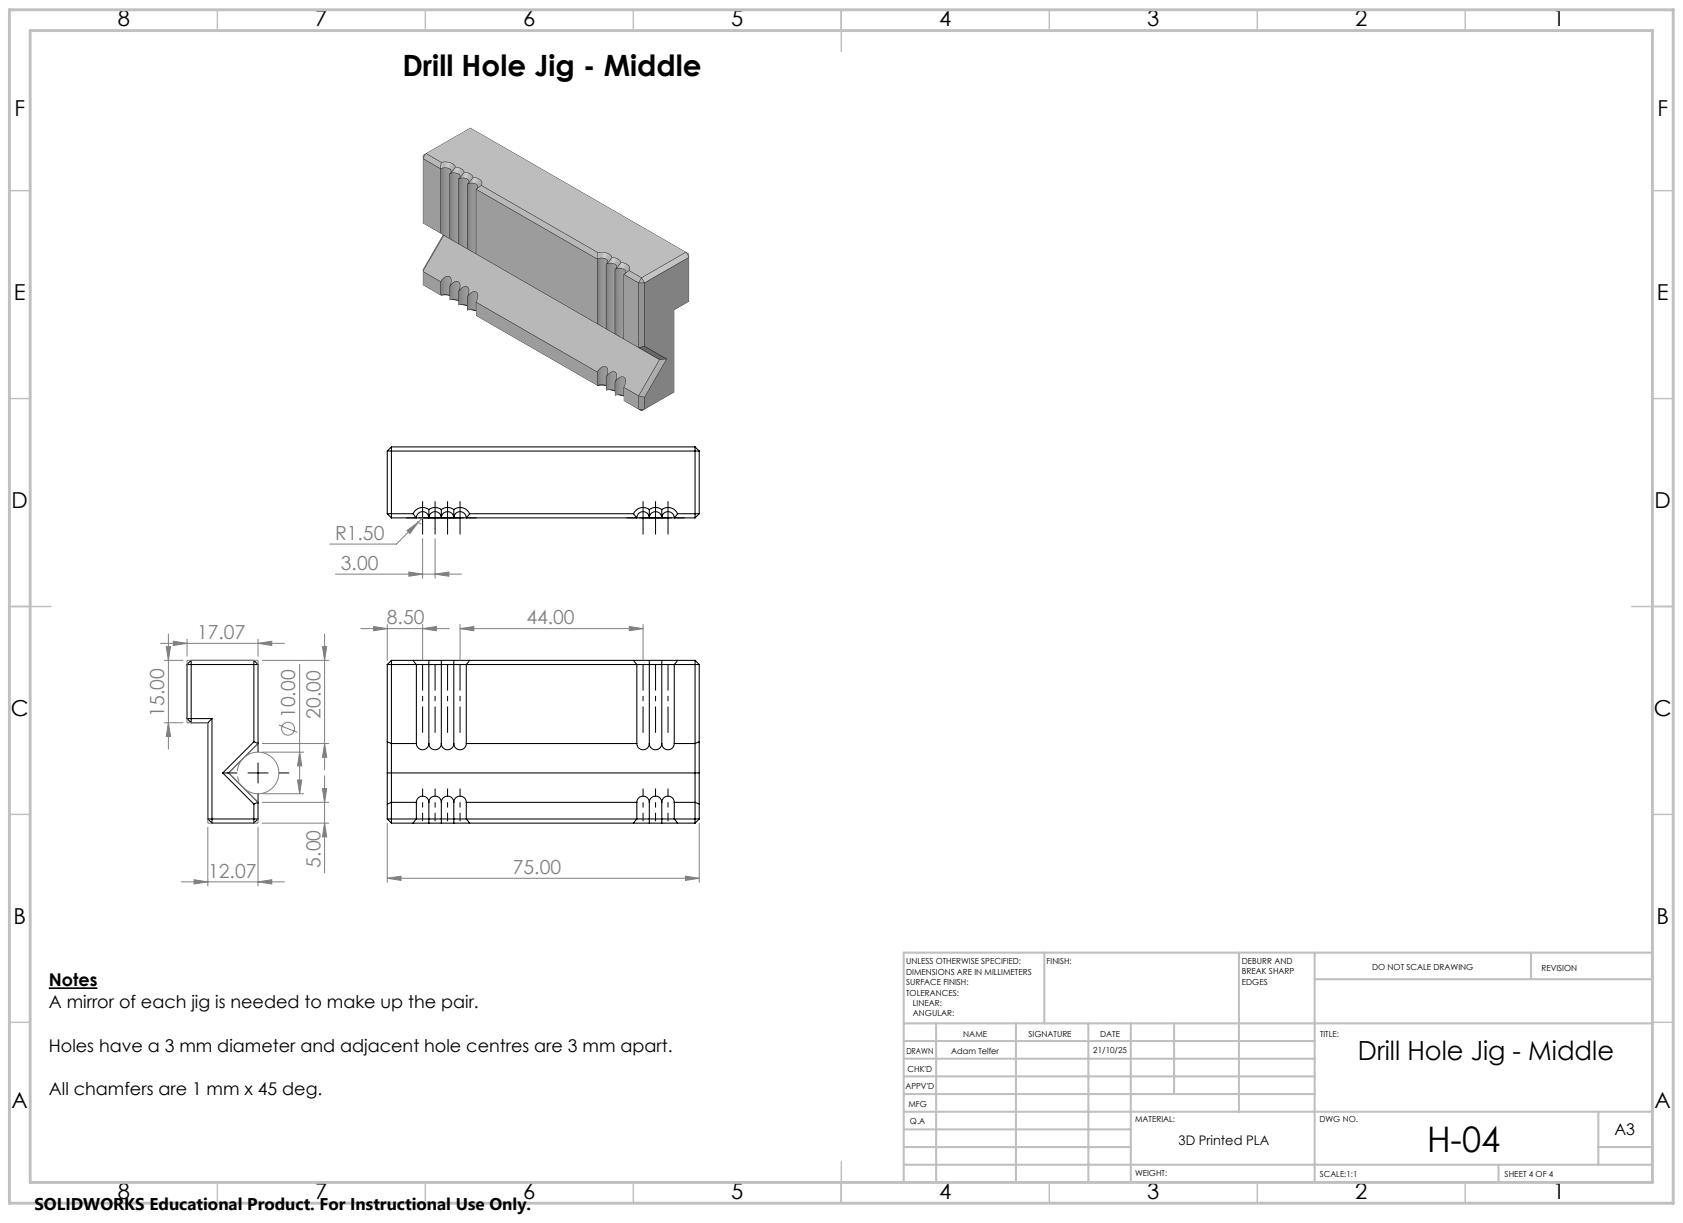
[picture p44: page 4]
FINISH:; DEBURR AND; BREAK SHARP; DO NOT SCALE DRAWING; REVISION

Drill Hole Jig - Middle

UNLESS OTHERWISE SPECIFIED:
DIMENSIONS ARE IN MILLIMETERS
SURFACE FINISH:
TOLERANCES:
LINEAR:
ANGULAR:

Notes
A mirror of each jig is needed to make up the pair.
Holes have a 3 mm diameter and adjacent hole centres are 3 mm apart.
All chamfers are 1 mm x 45 deg.

NAME | SIGNATURE | DATE | TITLE: Drill Hole Jig - Middle

DRAWN | Adam Telfer | | 21/10/25
CHK'D
APPV'D
MFG
